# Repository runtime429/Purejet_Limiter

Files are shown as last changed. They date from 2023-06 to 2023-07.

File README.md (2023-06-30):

# Purejet_Limiter

This repository contains a hardware design and software for a rev limiter for Ditech / Purejet Scooter.

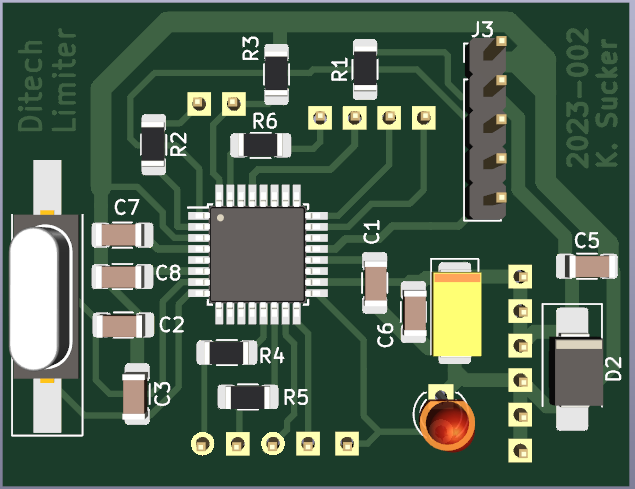
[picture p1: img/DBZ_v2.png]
Rev Limiter


principal author: Kevin Sucker

--------------------

# Intro

I am working on a rev limiter project utilizing the ATmega328P-AU microcontroller, similar to the Arduino Uno board. The purpose of this rev limiter is to simulate a lower value of the actual throttle valve, effectively restricting the engine's speed. It is designed to be inserted between the throttle and the ECU (Engine Control Unit).

To maximize the PWM (Pulse Width Modulation) output speed of the ATmega328P, I have opted for a 20 MHz quartz crystal, surpassing the standard 16 MHz crystal used in the Arduino Uno board.

In order to adjust the RPM limit, I have incorporated a teach button, allowing for easy customization of the rev limiter's speed threshold.

I have implemented a bypass feature that can disable the RPM limit when necessary. This can be achieved by using a cheap 433MHz remote control, such as the one available on AliExpress (http://aliexpress.com/item/1005003558907008.html), or by integrating a switch into the system.

# 3D printable housing

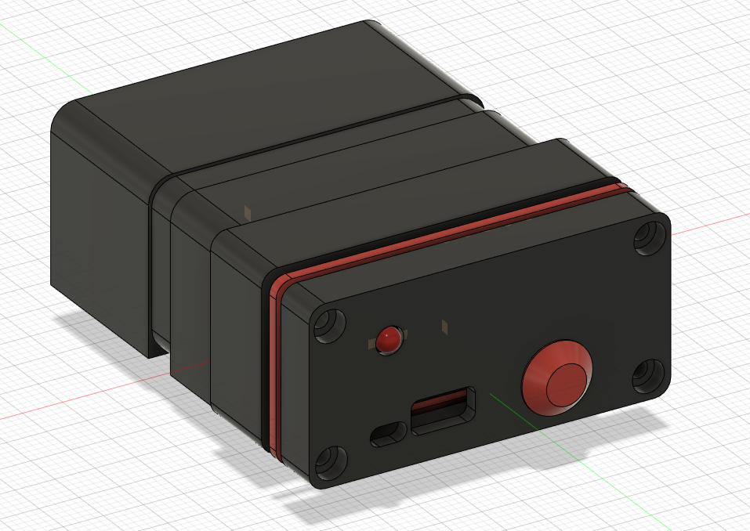
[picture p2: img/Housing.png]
Front View


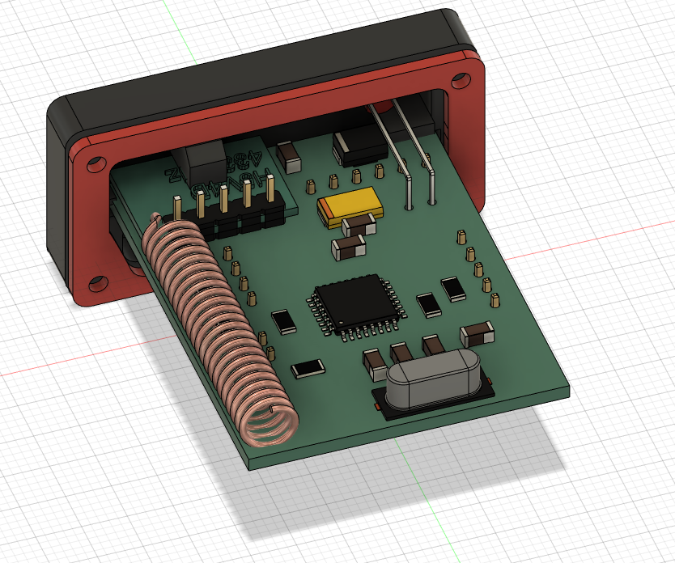
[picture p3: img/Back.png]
Back


# Etching the board and PCB assembly

Thanks to [Tobias Link on Youtube](https://youtu.be/-L1i9SnYGaU) for his excellent Tutorial!

Checkout [Build_PCB.md](https://github.com/runtime429/Purejet_Limiter/blob/main/PCB_make/Build_PCB.md)

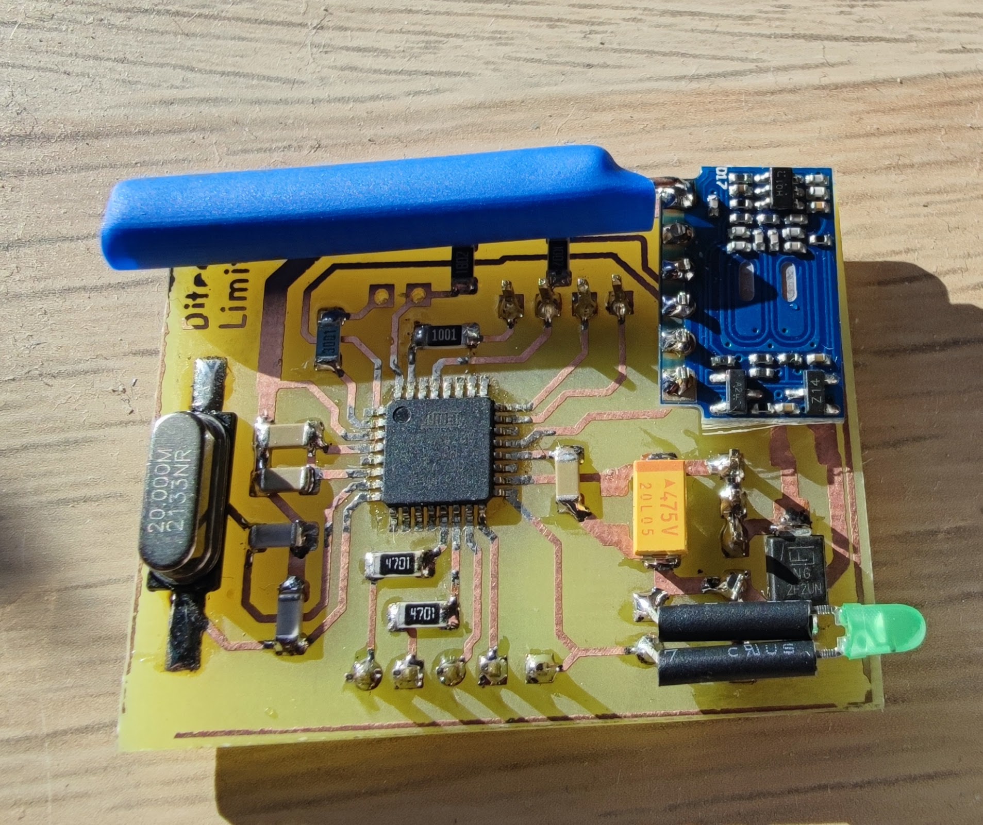
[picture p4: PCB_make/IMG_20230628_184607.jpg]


# How to flash the Board

- Add the [MiniCore](https://github.com/MCUdude/MiniCore) to your Arduino IDE
- Tools -> Bootloader -> No Bootloader
        -> Clock -> external 20Mhz
- Choose your ISP Programmer
- Download the [RCSwitch](https://github.com/sui77/rc-switch)-library from the arduino library manager
- Connect to the ISP Pins on the Board
- Burn Bootloader to set the Fuse-Bits
- Upload Sketch Using Programmer
- Press any key of your 433MHz remote
- You can read the value of yor 433MHz signal on the TX Uart pin (Baud 115200), I copiet the Signal from a [cheep 433MHz wireless socket remote](https://github.com/runtime429/Purejet_Limiter/blob/main/img/433_remote.png)
- Change the value of the "const int valRcSig", in my case to 21777
- Repload Sketch Using Programmer

# Limiter Installation on Scooter How-To

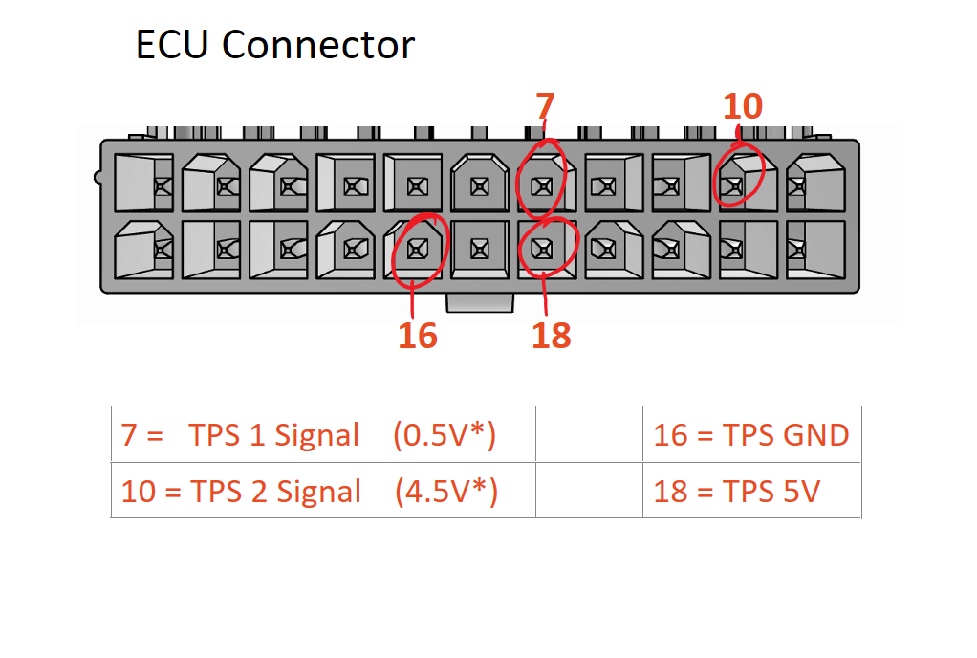
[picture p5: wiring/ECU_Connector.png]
Connector


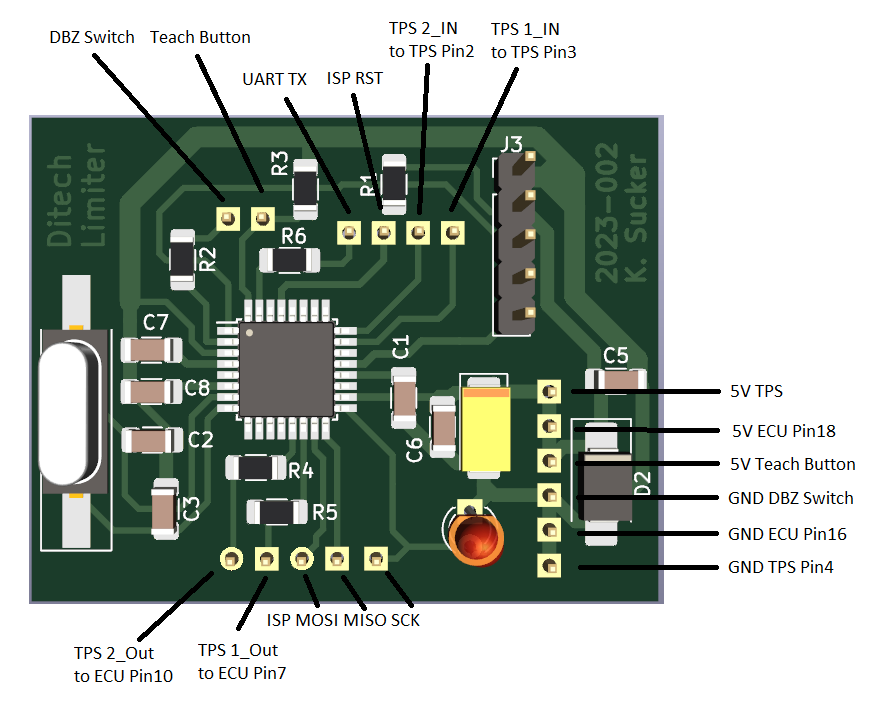
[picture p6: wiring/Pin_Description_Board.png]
Pin Description


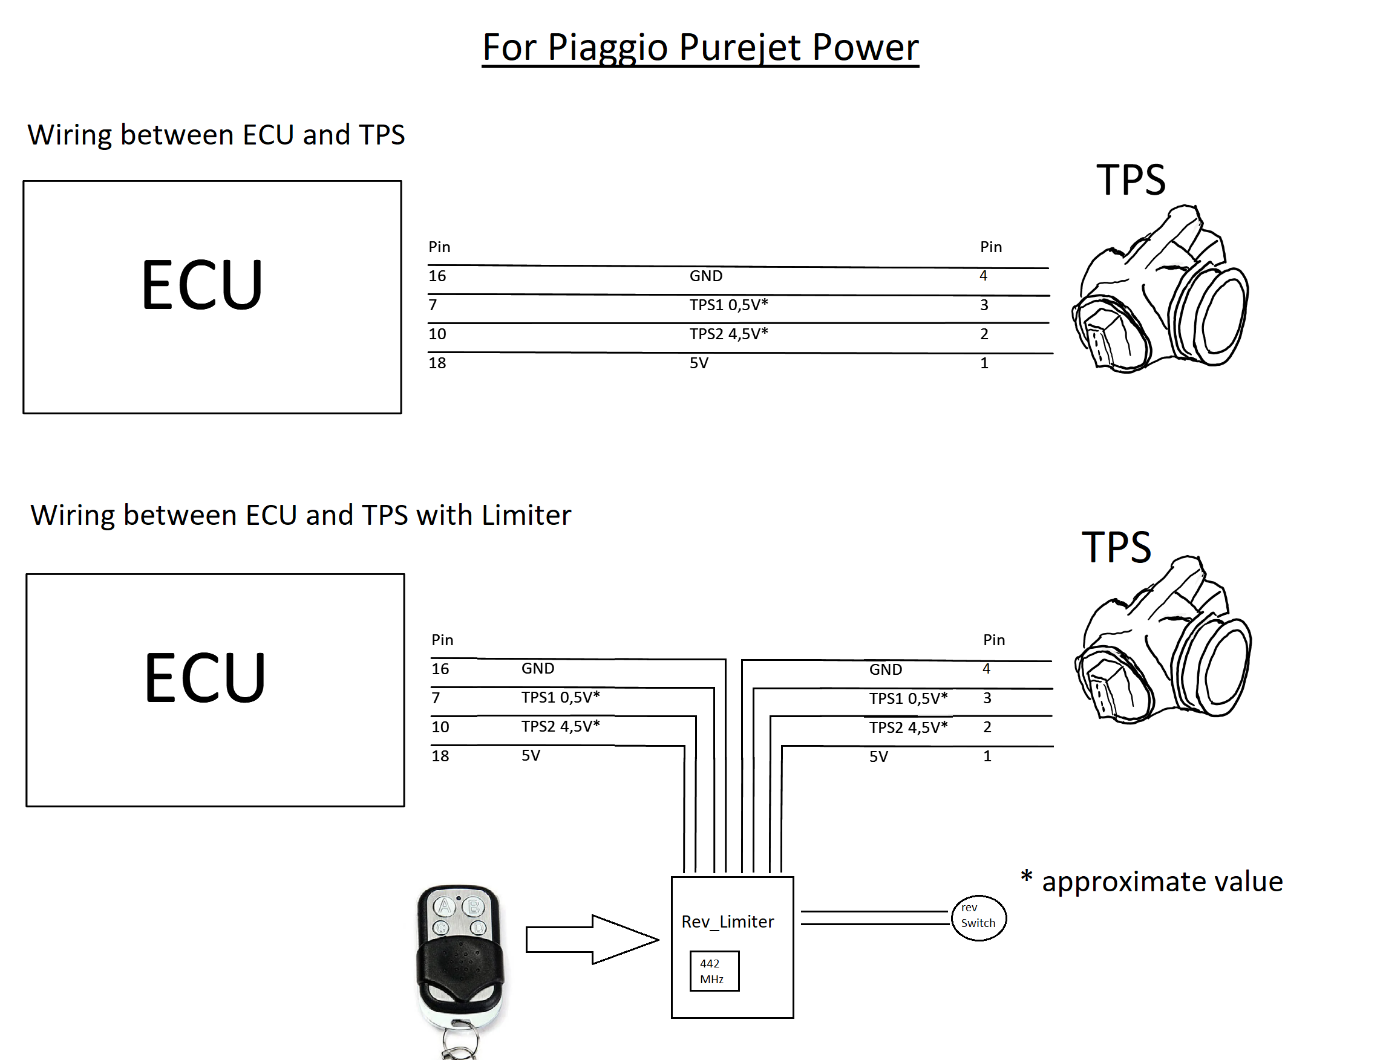
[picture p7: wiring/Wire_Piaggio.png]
Wiring


# Set up the Rev Limiter

Look at YouTube:

Rev (Speed) Limiter for Piaggio Gilera Aprilia - Purejet / Ditech (https://www.youtube.com/watch?v=lKDDaW2R90E)

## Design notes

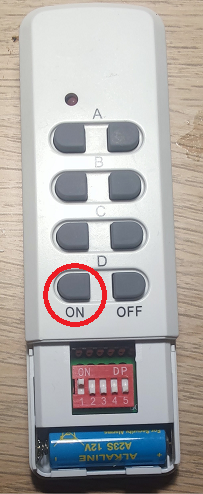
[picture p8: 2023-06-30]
img/433_remote.png

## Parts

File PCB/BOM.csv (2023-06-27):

ID | Bezeichner | Footprint | Stückzahl | Bezeichnung | Anbieter und Referenz
1 | J16,J11 | PinHeader_1x01_P2.54mm_Horizontal | 2 | PWR_GND
2 | J15 | PinHeader_1x02_P2.54mm_Horizontal | 1 | Conn_01x02_Pin
3 | J14 | PinHeader_1x01_P2.54mm_Horizontal | 1 | ISP_SCK
4 | J13 | PinHeader_1x01_P2.54mm_Horizontal | 1 | ISP_RST
5 | J12 | PinHeader_1x02_P2.54mm_Horizontal | 1 | ISP_MISO_MOSI
6 | J10 | PinHeader_1x01_P2.54mm_Horizontal | 1 | PWR_5V
7 | J9 | PinHeader_1x01_P2.54mm_Horizontal | 1 | DBZ_Switch_MCU
8 | J8 | PinHeader_1x01_P2.54mm_Horizontal | 1 | DBZ_Switch_GND
9 | J7 | PinHeader_1x01_P2.54mm_Horizontal | 1 | Teach_Button_VCC
10 | J6 | PinHeader_1x01_P2.54mm_Horizontal | 1 | Teach_Button_MCU
11 | J5 | PinHeader_1x01_P2.54mm_Horizontal | 1 | TPSi_VCC
12 | J4 | PinHeader_1x01_P2.54mm_Horizontal | 1 | UART
13 | J2,J1 | PinHeader_1x01_P2.54mm_Horizontal | 2 | Conn_01x01_Socket
14 | C3 | C_1206_3216Metric_Pad1.33x1.80mm_HandSolder | 1 | 22pf
15 | D1 | LED_D3.0mm | 1 | LED
16 | J3 | PinHeader_1x05_P2.54mm_Vertical | 1 | H5V4D
17 | C8,C7,C1 | C_1206_3216Metric_Pad1.33x1.80mm_HandSolder | 3 | 100nF
18 | R1 | R_1206_3216Metric_Pad1.30x1.75mm_HandSolder | 1 | 10k
19 | Y1 | Crystal_SMD_HC49-SD_HandSoldering | 1 | 20Hz
20 | U2 | TQFP-32_7x7mm_P0.8mm | 1 | ATmega328P-A
21 | C6,C5 | C_1206_3216Metric_Pad1.33x1.80mm_HandSolder | 2 | 1uF
22 | D2 | D_SMB_Handsoldering | 1 | SM6T100A
23 | R3 | R_1206_3216Metric_Pad1.30x1.75mm_HandSolder | 1 | 22k
24 | C4 | CP_EIA-6032-15_Kemet-U_Pad2.25x2.35mm_HandSolder | 1 | 4,7uF
25 | C2 | C_1206_3216Metric_Pad1.33x1.80mm_HandSolder | 1 | 22pF
26 | R4 | R_1206_3216Metric_Pad1.30x1.75mm_HandSolder | 1 | 4,7k
27 | R5 | R_1206_3216Metric_Pad1.30x1.75mm_HandSolder | 1 | R
28 | R2,R6 | R_1206_3216Metric_Pad1.30x1.75mm_HandSolder | 2 | 1K
29 | * | H5V4D | 1 | H5V4D

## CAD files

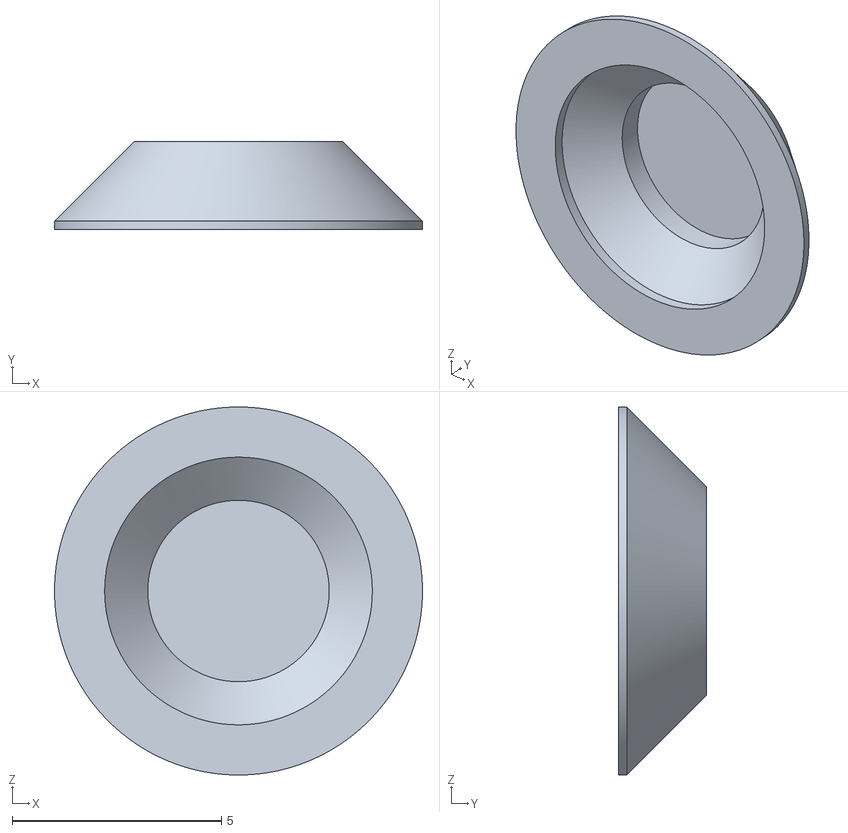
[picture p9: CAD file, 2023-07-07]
STL/Button_protection.stl
8.80 x 2.10 x 8.80

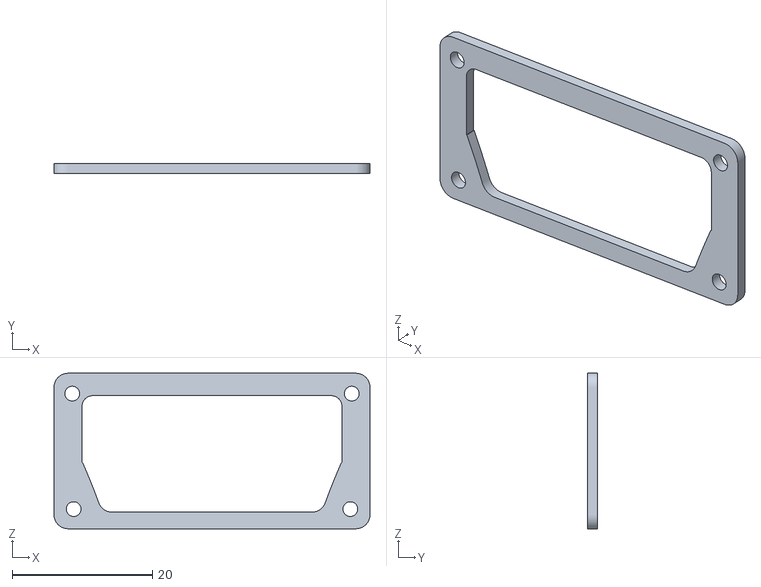
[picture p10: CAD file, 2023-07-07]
STL/Seal.stl
45.0 x 1.40 x 22.2

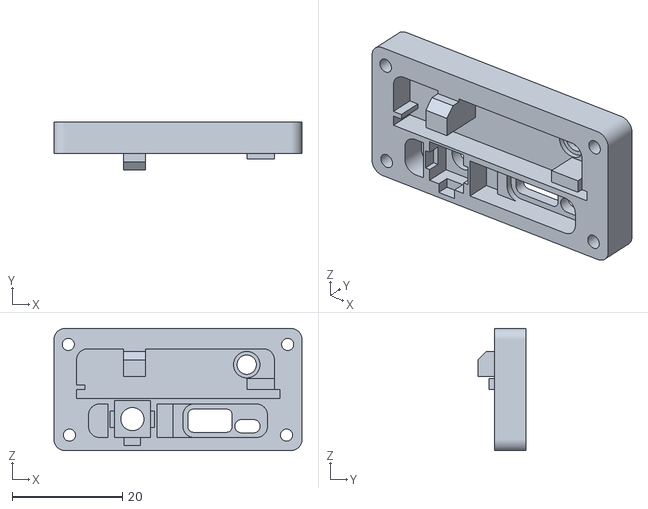
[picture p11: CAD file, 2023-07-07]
STL/Cover.stl
45.0 x 8.80 x 22.2

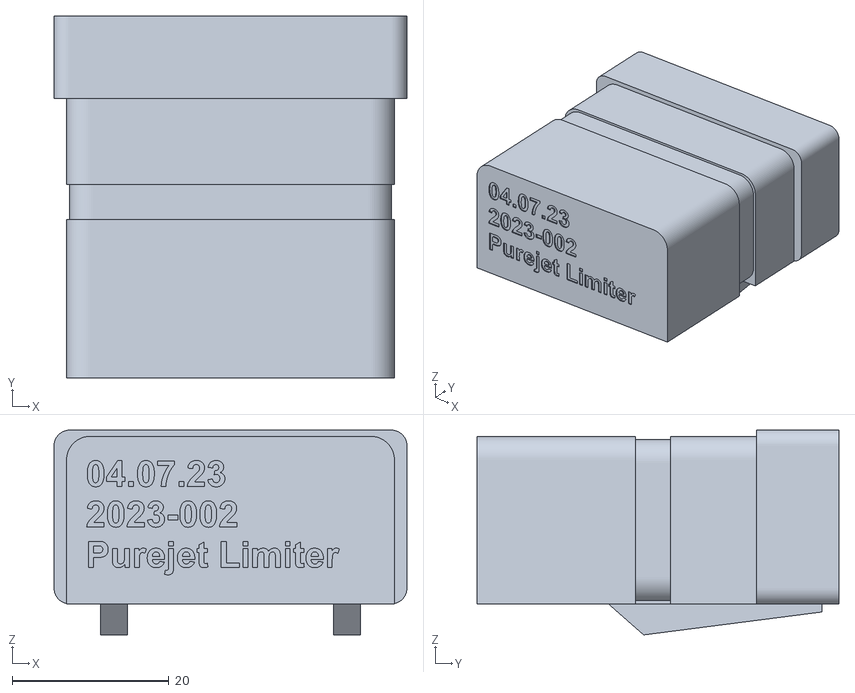
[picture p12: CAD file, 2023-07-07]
STL/Case.stl
45.0 x 46.2 x 26.1

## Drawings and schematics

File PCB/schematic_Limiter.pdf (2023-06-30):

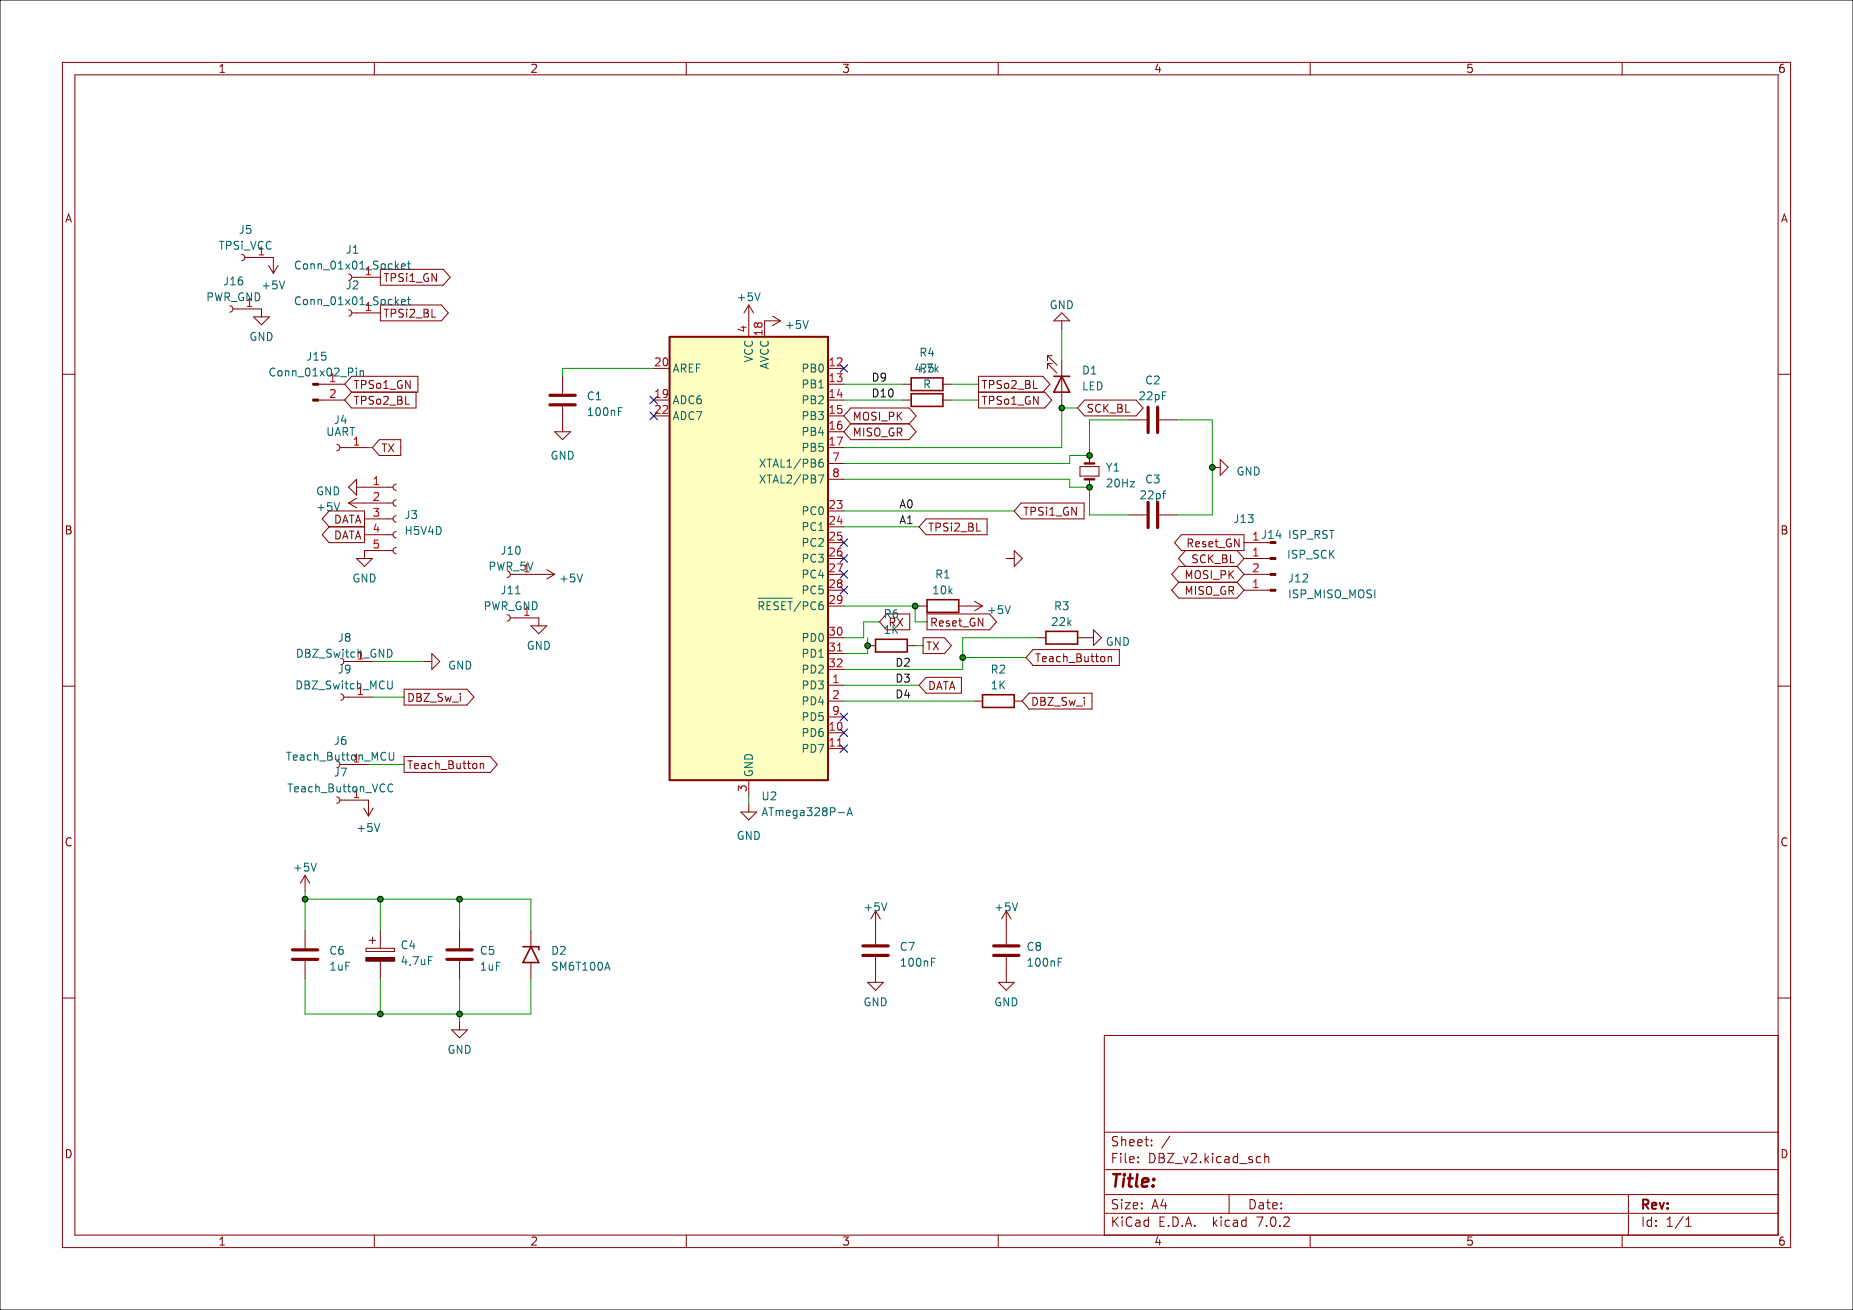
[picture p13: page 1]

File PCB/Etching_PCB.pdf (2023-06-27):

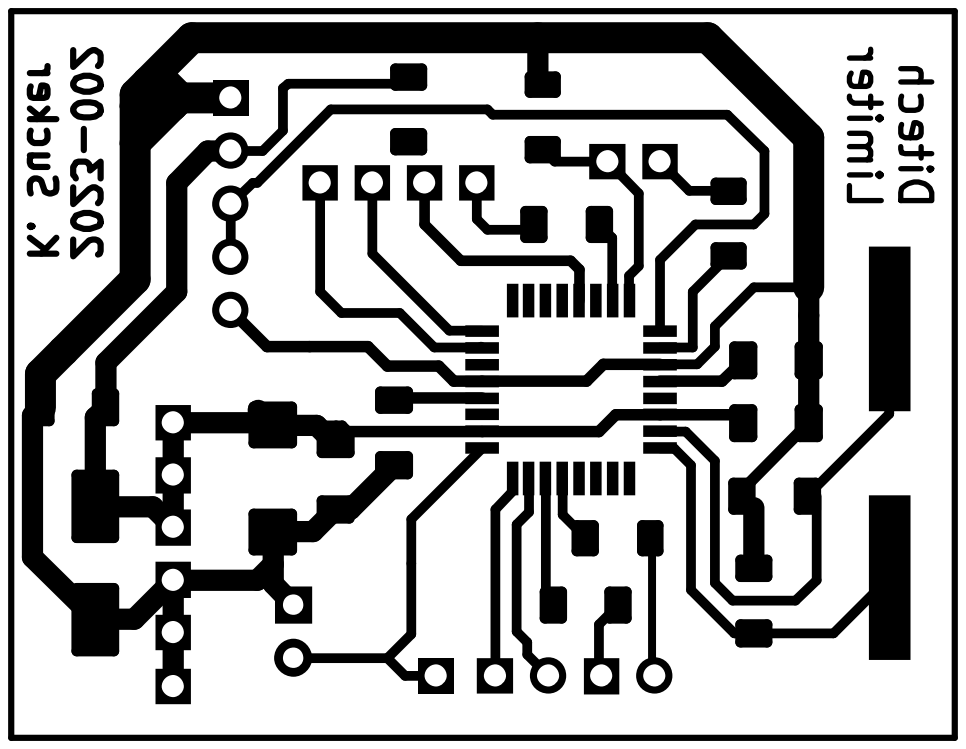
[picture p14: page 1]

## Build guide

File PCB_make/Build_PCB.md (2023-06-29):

# Etching the Layout

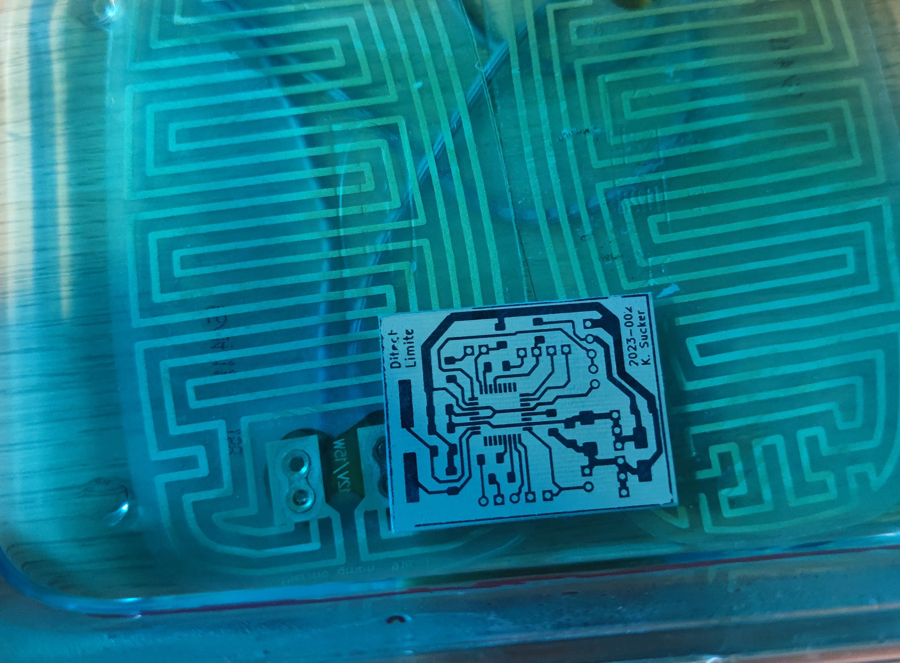
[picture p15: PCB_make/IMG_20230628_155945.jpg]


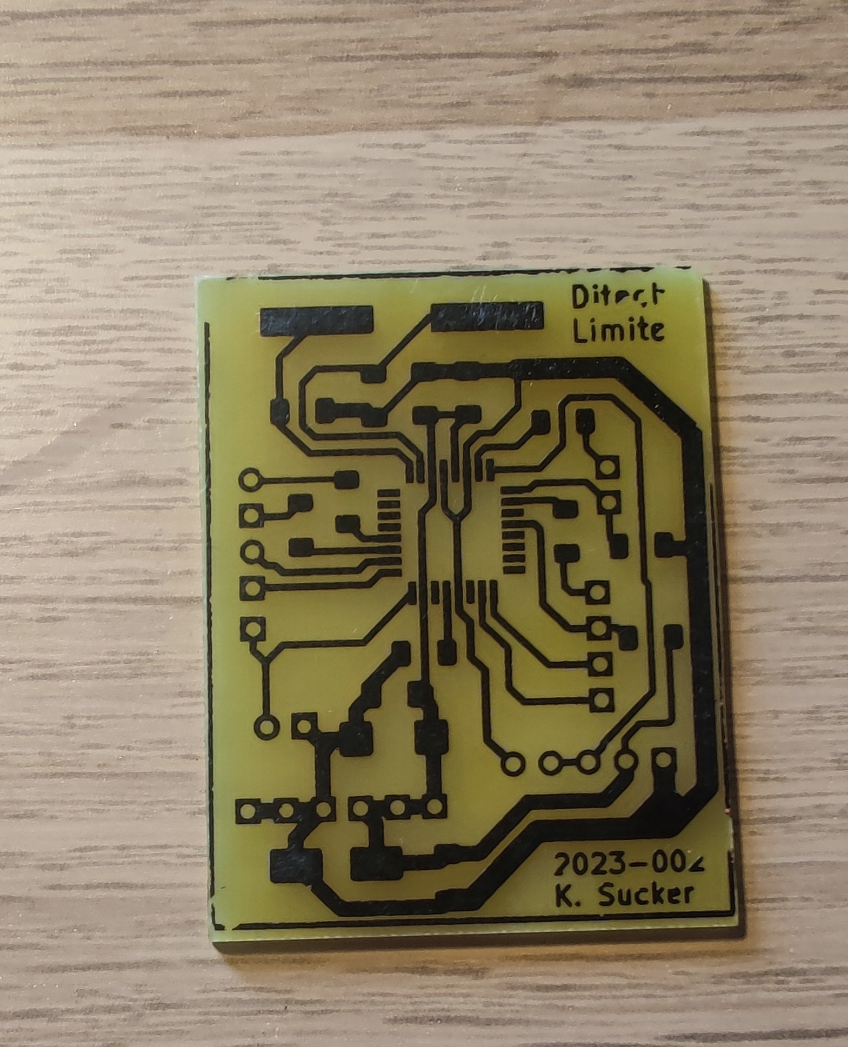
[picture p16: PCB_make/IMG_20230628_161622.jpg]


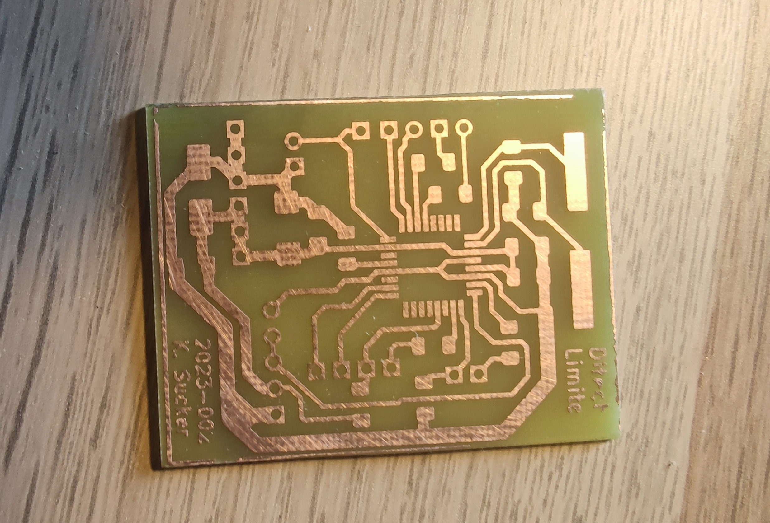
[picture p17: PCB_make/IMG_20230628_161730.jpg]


# Solder it



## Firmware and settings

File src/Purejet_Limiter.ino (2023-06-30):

#include <EEPROM.h>
#include <RCSwitch.h>

const int TPSo1 = 10;    // OUTPUT TO TPS
const int TPSo2 = 9;   // OUTPUT TO TPS

const byte TPSi1 = A0;  // INPUT OF TPS
const byte TPSi2 = A1;  // INPUT OF TPS

const int receivePin = 1;     // Remote receive interrupt Pin
const int valRcSig = 21777;    // Value of rc remote signal for receive

bool rcSwitch = false;        // State of rc Switch
int valrc = 0;                // Value of remote signal if no Signal received

const int teachPin = 2;       // Teach button
const int ledPin = 13;        // Toggle LED teach-mode

const int revPin = 4;         // rev_limit_switch
bool revPinState;             // state of rev_limit_switch
int ledState = LOW;           // current state of the output pin
int buttonState;              // current reading from the input pin
int lastButtonState = LOW;    // previous reading from the input pin
int lastDebounceTime = 0;     // last time the output pin was toggled
int debounceDelay = 50;       // debounce time

int adc0, adc1;           // variables to read input of TPS
int adcsetup0, adcsetup1; // variables to read input of TPS on Setup

int maxadc0 = 0;        // lowest value in teach mode

int revlv1; // variables of Voltage limiter to ECU
float limitfactor;      // Limit factor to output

RCSwitch mySwitch = RCSwitch();

void setup() {
  
  TCCR1B = TCCR1B & B11111000 | B00000001;    // set timer 1 divisor to 1 for PWM frequency of 31372.55 Hz for D9 & D10

  adcsetup0 = analogRead(TPSi1);    // read value of TPS1 0,5V
  adcsetup1 = analogRead(TPSi2);    // read value of TPS2 4,5V
  analogWrite(TPSo1, adcsetup0 / 4);     // set TPS1 value to ECU output voltage
  analogWrite(TPSo2, adcsetup1 / 4);     // set TPS2 value to ECU output voltage

  pinMode(teachPin, INPUT);
  pinMode(ledPin, OUTPUT);
  pinMode(revPin, INPUT_PULLUP);

  
  Serial.begin(115200);
  revlv1 = read_int(0);     // read value of TPS1 limit from EEPROM


  mySwitch.enableReceive(receivePin); // Receiver on interrupt 0 => that is pin #2


  limitfactor = (100.00 / map(revlv1, adcsetup0, adcsetup1, 0, 100) + 2);

  digitalWrite(LED_BUILTIN, HIGH);   // turn the LED on (HIGH is the voltage level)
  delay(1000);                       // wait for a second
  digitalWrite(LED_BUILTIN, LOW);    // turn the LED off by making the voltage LOW

  while (adcsetup0 > adcsetup1) {   // TPS Signal is twisted
  blinkLED(100, 100);     // LED blinks on for 100 milliseconds, then off for 100 milliseconds
  blinkLED(500, 500);     // LED blinks on for 500 milliseconds, then off for 500 milliseconds
}

}

void loop() {

  revPinState = digitalRead(revPin); // if no RC_connected

  teach_tps_toggle();
  
  if (ledState == HIGH) {
    if (maxadc0 < adc0) maxadc0 = adc0;
  }
  
  if (valrc != valRcSig) {
    received_remote();
  }

  adc0 = analogRead(TPSi1);     // read value of TPS1
  adc1 = analogRead(TPSi2);     // read value of TPS2
  
  if (valrc == valRcSig || revPinState == LOW) {
    analogWrite(TPSo1, adc0 / 4);     // set TPS1 value to ECU output voltage
    analogWrite(TPSo2, adc1 / 4);     // set TPS2 value to ECU output voltage
  } else {
    analogWrite(TPSo1, ((adc0 - adcsetup0) / limitfactor + adcsetup0) / 4);
    analogWrite(TPSo2, (adcsetup1 - (adcsetup1 - adc1) / limitfactor) / 4);
  }
 
}

void received_remote() {
  if (mySwitch.available()) {
    valrc = mySwitch.getReceivedValue();
    Serial.print("Received ");
    Serial.print(valrc);
    Serial.print(" / ");
    Serial.print(mySwitch.getReceivedBitlength());
    Serial.print("bit ");
    Serial.print("Protocol: ");
    Serial.println(mySwitch.getReceivedProtocol());
    mySwitch.resetAvailable();
  }
}

void write_int(int address, int value) {
  byte byte_2 = (value & 0xFF);
  byte byte_1 = ((value >> 8) & 0xFF);
  EEPROM.update(address, byte_2);
  EEPROM.update(address + 1, byte_1);
  Serial.print("Write to EEPROM (Address: ");
  Serial.print(address);
  Serial.print(",");
  Serial.println(value);
}

int read_int(int address) {
  long byte_2 = EEPROM.read(address);
  long byte_1 = EEPROM.read(address + 1);
  int val = ((byte_2 << 0) & 0xFFFFFF) + ((byte_1 << 8) & 0xFFFFFFFF);
  Serial.print("Read from EEPROM (Address: ");
  Serial.print(address);
  Serial.print(",");
  Serial.println(val);
  return val;
}

void blinkLED(int onTime, int offTime) {
  digitalWrite(LED_BUILTIN, HIGH);   // turn the LED on (HIGH is the voltage level)
  delay(onTime);                     // wait for a certain time
  digitalWrite(LED_BUILTIN, LOW);    // turn the LED off by making the voltage LOW
  delay(offTime);                    // wait for a certain time
}

void teach_tps_toggle() {
  int reading = digitalRead(teachPin);    // read the state of the switch into a local variable
  
  if (reading != lastButtonState) {     // check if the switch state has changed
    lastDebounceTime = millis();        // reset the debounce timer
  }
  
  if ((millis() - lastDebounceTime) > debounceDelay) {    // check if debounce delay has passed
    if (reading != buttonState) {       // check if button state has changed
      buttonState = reading;
      
      if (buttonState == HIGH) {        // toggle LED if the new button state is HIGH
        ledState = !ledState;
        Serial.println(ledState);
        
        if (ledState == HIGH) {
          Serial.println("Teaching TRUE");
        } else {
          write_int(0, maxadc0);
          maxadc0 = 0;            // reset to lowest value in teach mode for next teach
          Serial.println("Teaching End");
          revlv1 = read_int(0);     // read value of TPS1 limit
          Serial.println("Set new values from EEPROM to var");
          limitfactor = (100.00 / map(revlv1, adcsetup0, adcsetup1, 0, 100) + 2);
          Serial.print("Set limitfactor:");
          Serial.println(limitfactor);
        }
      }
    }
  }
  
  digitalWrite(ledPin, ledState); // set the LED according to the ledState value
  lastButtonState = reading;      // save the reading. Next time through the loop, it'll be the lastButtonState

}
